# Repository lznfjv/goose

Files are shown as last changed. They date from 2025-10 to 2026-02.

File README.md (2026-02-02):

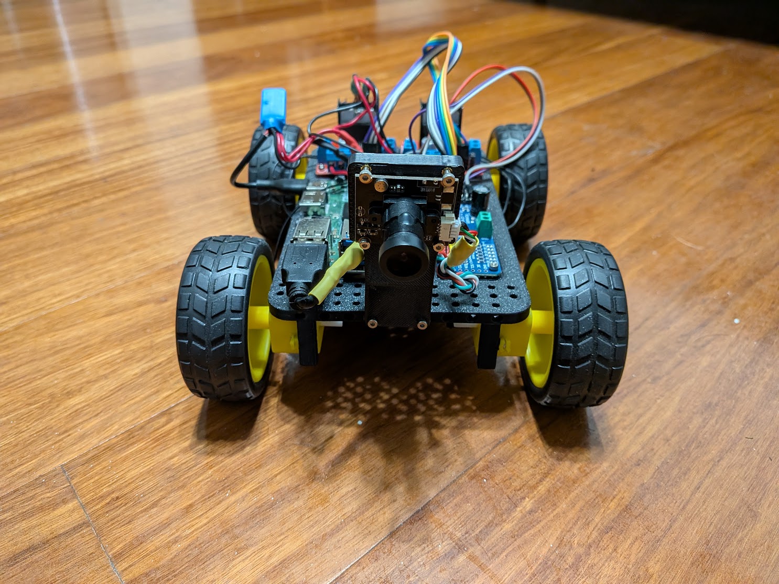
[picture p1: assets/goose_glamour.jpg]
Goose Glamour Shot


# GooseBot - A hands-on, up-to-date instructional platform for robotics
Author: Kevin Racktoo

## Problem
There is a startling lack of robotics kits on the market which effectively guide students through the process of constructing and programming a modern robot.
Sure, there are options that provide opportunities for low-level programming of servos and motors, and others that demonstrate basic computer vision filtering techniques.
However, very few kits present the opportunity to thoroughly understand every element of the modern robot. GooseBot, or simply Goose, is an in-development project, designed to be
the ideal educational robotics kit, providing experience with real-world technologies that sticks because the procedures employed are exactly those used in the real-world.

## Objective
The GooseBot project kit will encompass the following topics with the objective of creating an autonomous ground-vehicle robot which closely emulates the functionality of a self-driving car.
- Hardware selection
-   Sensors
-   Chassis
-   Mechatronics
-   Power system
- Computer vision techniques
- Hardware acceleration using NPU
- Programming control of mechatronic components
- Sensor fusion

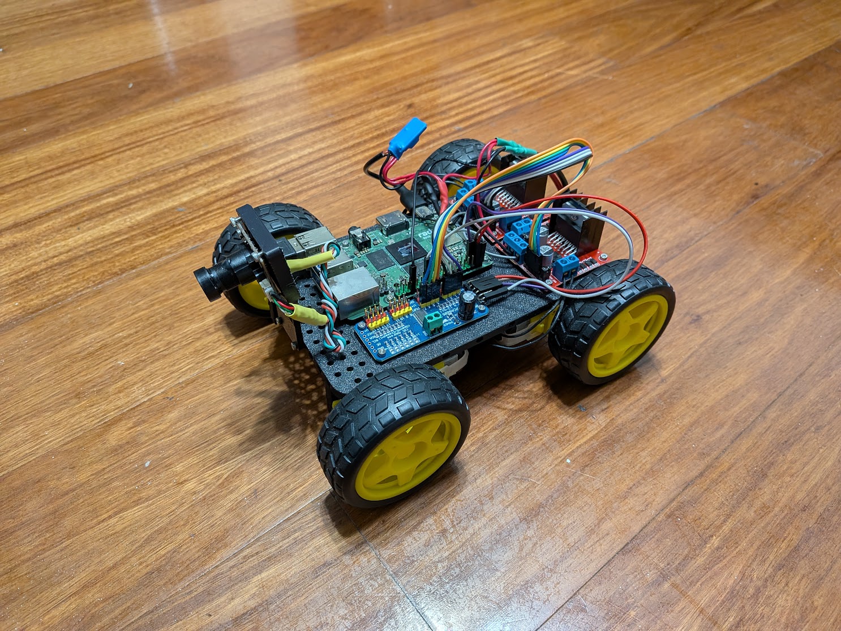
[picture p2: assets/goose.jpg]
Goose


# Progress
See the respective subsections in this repo for further information.

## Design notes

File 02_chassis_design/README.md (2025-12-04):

# Parameters
The chassis of the robot will be designed such that
- All selected components are easily mounted/unmounted
- The chassis is easily reproduced using any ordinary 3D printer
- Impact will not damage the frame
- Weight will not prevent the motors from functioning as expected
- Ventilation prevents overheating of any temperature-sensitive components

# Chassis

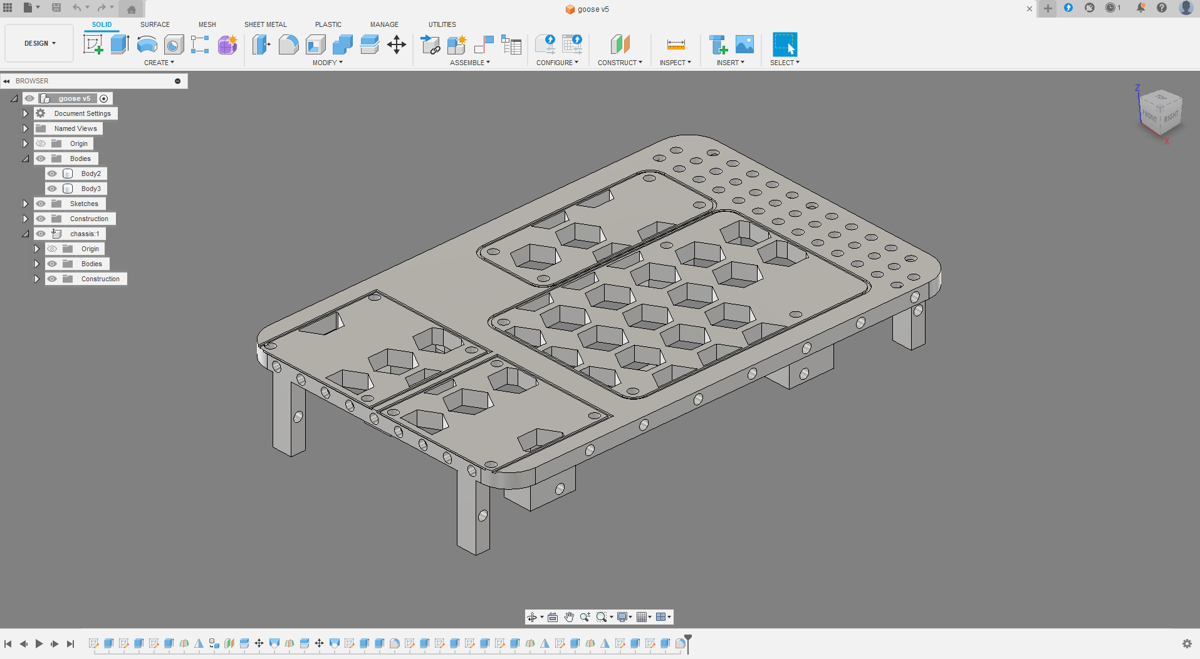
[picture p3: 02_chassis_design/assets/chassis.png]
Goose V5 Chassis


This was created in Autodesk Fusion, and designed for easy printing on most common 3D printers. I've used ASA for its strength and UV resistance, but this could just as easily be produced with ABS or even PLA. The Fusion archive file is provided for easy modification, but the STEP file should be all you need to print.

Lots of mounting holes are available, sized for M2 heat-set inserts. Heat-set inserts will allow the user to mount and unmount components as many times as they would like without worry of wearing out the threading on the 3D print itself. The inserts I use can be found here:
https://www.amazon.com/dp/B088QJG676

Each of the primary selected components has its own designated spot, with measurements taken to ensure precise mounting and no additional strain on the components.

# Camera Mount

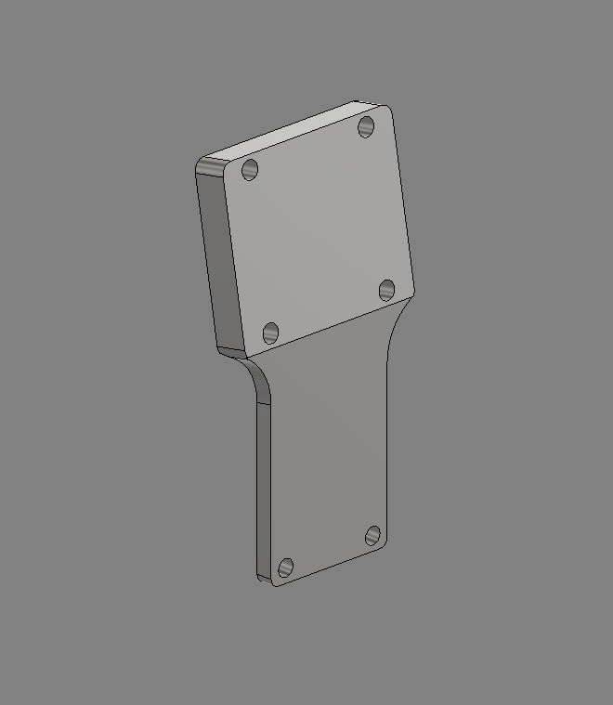
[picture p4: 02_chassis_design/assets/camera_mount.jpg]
Camera Mount


Additionally, I've provided a camera mount that was designed for the de-housed camera sensor module from the USB webcam linked in the previous chapter.

This mount is designed to be attached to the front of the Goose Chassis v5 using M2 screws and the aforementioned heat-set inserts. Heat-set inserts can also be used on the upper setion of the mount to retain the camera module, or hex nuts can be used at the rear of the mount to secure the module.

The Fusion (.f3d) archive file is provided such that you may modify the mount to fit any other camera modules if desired.

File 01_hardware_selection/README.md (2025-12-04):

# Parameters
The hardware for GooseBot is selected to meet the following parameters.

- Low cost - As this kit is to be used by students and educators, the complete bill of materials should not exceed $100 USD at the time of writing this document. As some components will be slightly lower-cost in bulk, I will allow the limit to be exceeded whenever bulk orders are cheaper or there are lower-cost alternatives available. Additionally, much of these components will already be on-hand, but the comprehensive bill of materials summary at the end of this document will include some of those, too.
- Comparable performance to DuckieBot - The DuckieBot is centered around the Nvidia Jetson Nano 4GB. The Nano *was* a capable device in its prime due to its onboard GPU, allowing for acceleration of computer vision processing using CUDA libraries. Today, many more affordable alternatives exist, utlizing Neural Processing Units (NPUs). Likewise, devices with faster processors, more memory, and wider arrays of peripherals are available. At the very least, GooseBot should be able to perform as well as DuckieBot; at best, it will perform far better.
- Up-to-date software - My greatest gripe with the DuckieBot, and with Jetson Nano's in general, is the use of completely obsolete software. Nvidia requires the use of its own customized version of Ubuntu 18.04 on the Jetson Nano as it has not updated the Linux kernel to allow hardware acceleration on its custom Tegra CPU architecture. This makes the development and modification of software on the DuckieBot a collossal pain; my Embedded Control class has spent *weeks* debugging and troubleshooting software that should be nearly plug-and-play.
- Widespread availability - The components selected should be easily purchaseable from reliable distributors such as Mouser and DigiKey. Where this is impractical, the components must be easily substitutable.

# Single-board Computer (SBC)
To meet the *comparable-performance* parameter, the single-board computer selected as the core component of GooseBot should have 
- at least 4GB of RAM (preferably the faster, higher-bandwidth LPDDR5)
- NPU with operating speed of at least 3TOPs
- WiFi to take the place of the external USB WiFi dongle used on the Jetson Nano
- USB ports for peripherals
- MicroSD expandable storage
- Common communication interfaces on GPIOs (I2C, SPI, PWM, Analog, etc.)
- Up-to-date software support (Ubuntu LTS for next two years minimum)

The SBC selected to meet these criteria is the Radxa Rock5c Lite. Its characteristics are given:
- Rockchip RK3582 hexa-core CPU
- Anywhere between 2 and 32GB of LPDDR4x RAM
- MicroSD expandable storage
- 5TOPS NPU
- Identical GPIO as the Raspberry Pi and Jetson Nano
- WiFi and Bluetooth in-built
- USB2 and USB3
- Native support for Ubuntu 20 and 22

The specific model I am using can be found here for $65, with 4GB of RAM.
https://www.amazon.com/Radxa-ROCK-5C-RK3588S2-4GB/dp/B0CYY1R9ZH

# Motors and Wheels
We want a DC motor setup for simple, effective control. Motor+gearbox assemblies almost identical to those onboard the DuckieBot are available in entire kits for <$20. This is the kit I will be using:
https://www.amazon.com/dp/B08JLYY77W

This comes with wheels, motors, gearboxes, and H-bridge motor driver modules.

# Sensors
## Camera
The foremost sensor on the platform is the camera module. Rather than a typical CSI camera module which ranges in cost from $20 to $100, a simple USB webcam with a wide field-of-view can be used, with the same or better optical performance. Furthermore, many USB webcams are coupled with onboard microphones, which enables development of audio processing features. The component selected is this:
https://www.amazon.com/dp/B0F7Y6JLM7

## Time-of-Flight
In addition to the computationally-expensive visual processing system that the robot will use, time-of-flight sensors can be employed at the front and sides of the robot for compact, resource-constrained proximity sensing and obstacle avoidance. Again, these can be found at extremely low costs. This set of three units can be had for just $10.
https://www.amazon.com/dp/B0B6ZT7NRW

# Middleware
For simplified integration of sensors and drive components, it is useful to have a PWM-I2C interface. This way, we can offload the PWM signal generation that will be used to vary speeds of the motors to a designated component, rather than having to consume valuable CPU cycles of the SBC on such a tedious, repetitive tasks. Furthermore, servos and additional PWM-driven robotic components can easily be added without regard for the limited number of PWM pins on the SBC. I'm using this board, which has numerous alternatives available from various sellers on Amazon and DigiKey. The set I purchased includes two modules, and is $10.
https://www.amazon.com/dp/B0CNVBWX2M

# Power System
We need to be able to provide adequate power to all drive components while also maintaining a continuous 5V at 2.5A for the SBC. 

## Batteries
Lithium-ion batteries are the status-quo for robotics projects like these. A 3S (11.1V nominal) LiPo will be perfect. This instance is a bit more costly than I'd like for this project, but suitable alternatives can be found at hobby shops and RC drone suppliers for even cheaper.
https://www.amazon.com/dp/B07DNQMRWW

## 5V DC/DC Converter
As the 3S battery will output just under 13V at full charge, we need to drop this down to 5V for the SBC and sensors, and regulate that voltage to prevent brown-outs. There are tons of suitable DC/DC converters available, and I happened to have a few that would do on hand. Here's a set of six such DC/DC converters for around $14, that we can adjust to output the 5V that we'll need.
https://www.amazon.com/MP1584EN-DC-DC-Converter-Adjustable-Module/dp/B01MQGMOKI

# Bill of Materials (BoM Summary)

Here are all of updated materials in a convenient table, for ordering (costs as of 12/03/2025). Some of these parts, such as assembly hardware, are optional. Additionally, many arrive as kits or sets that can be used for more than one robot. It is only assumed that the builder already possesses a 3S LiPo balance charger, wire, dupont jumper wires, a soldering station, and heatshrink/electrical tape.

| Category | Item | Specs/Notes | Cost | Source |
| :--- | :--- | :--- | :--- | :--- |
| **SBC** | **Radxa Rock5c Lite** | 4GB RAM, 5TOPS NPU, WiFi/BT | **$66.99** | [Amazon Link](https://www.amazon.com/Radxa-ROCK-5C-RK3588S2-4GB/dp/B0CYY1R9ZH) |
| **Motors** | **DC Motor Kit** | Includes wheels, gearboxes, drivers | **$15.99** | [Amazon Link](https://www.amazon.com/dp/B08JLYY77W) |
| **Sensors** | **USB Webcam** | USB connector, onboard mic | **$9.99** | [Amazon Link](https://www.amazon.com/Diccik-Webcams-Correction-FaceTime-Hangouts/dp/B0F2Z2DXW3) |
| **Sensors** | **Time-of-Flight** | Set of 3 units, prox/obstacle | **$9.99** | [Amazon Link](https://www.amazon.com/dp/B0B6ZT7NRW) |
| **Middleware**| **PWM-I2C Board** | Set of 2, Servo/Motor control | **9.99** | [Amazon Link](https://www.amazon.com/dp/B0CNVBWX2M) |
| **Power** | **3S LiPo Battery** | 11.1V Nominal | **29.69** | [Amazon Link](https://www.amazon.com/dp/B07MQT6YJN) |
| **Power** | **DC/DC Converter** | Set of 6, Adjustable (13V -> 5V) | **$12.25** | [Amazon Link](https://www.amazon.com/MP1584EN-DC-DC-Converter-Adjustable-Module/dp/B01MQGMOKI) |
| **Assembly** | **M2 Heat-set Inserts** | Optional, More convenient mounting | **$8.99** | [Amazon Link](https://www.amazon.com/dp/B088QJG676) |
| **Assembly** | **Hardware** | M2 Assorted screws | **$8.99** | [Amazon Link](https://www.amazon.com/dp/B0D3X33XGB) |
| | | **Total Estimate:** | **$172.87** | |

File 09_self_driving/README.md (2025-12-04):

Goose

# Bringing it All Together
So far, we have a severely over-powered RC car that also happens to run an object detection model. Now, we can synthesize those two featuresets into a rudimentary self-driving car algorithm.

This section assumes that you have a model town set up, with dashed yellow lane divider lines and solid white outer lane boundary lines. You can also add some red stop bar lines here and there if you want to see your robot politely pause at the stop bars before proceeding on its merry way.

The code for this lane-following system is provided for you in the drive.py script. Here, I will break down what each part of the code is doing.

**NOTE:** This is a cobbled-together lane-following and object-detection script that demonstrates an extremly basic mechanism for having a robot autonomously follow lanes. It is far, *far* from perfect, and may be observed occasionally losing its place and giving up on lane following if it encounters something it doesn't expect. Please feel free to build on this as you please, or tear it apart and start over. It is only provided to demonstrate essential capabilities and as a reference for further development.

# Script Set-up
For convenience, let's place the drive.py script in the same `yolodetect` directory we created in chapter 6. Also, make sure your `yolovenv` Python virtual environment is active, so that we know we have an environment that is set up to run object detection models on the NPU. As a refresher:

Deactivate any existing Python venv.

    deactivate

Change directory to your home folder.

    cd ~

Activate the `yolovenv` virtual environment then enter the `yolodetect` folder.

    source yolovenv/bin/activate
    cd yolodetect

Copy the `drive.py` file into this directory, if you haven't already.

We also need to install the Python packages that we previously used for motor testing, as the same packages are used by the script to maneuver the robot.

    pip install board adafruit-blinka adafruit-circuitpython-pca9685 gpiod adafruit-circuitpython-pca9685

# Run the Script
Let's run the script and see how it behaves. Before sending Goose into action, place it in the outer lane of your model town's road, in between the yellow dashed and white solid lines.

Next, make sure that the script knows where to find your RKNN model folder. Edit line 11 in `drive.py` to point to the correct model path.

To run the script:

    python drive.py

Goose should start to move, and the terminal should present you with a URL where you can view the object-detection model's hits in near-real-time. 

# Analysis
Let's go through the code. 

## Imports
Lines 1-9 are the same imports we've been using thus far, loading relevant Python packages and libraries for the peripherals we've connected, like the I2C-to-PWM bridge module.

## Config
Lines 10-18 expose some essential configuration parameters. We set the model path, then define the axis sizes for the video feed. This is pre-set to 640x480, because this is low-resolution enough for the NPU to run inferences rapidly while maintaining high enough resolution to clearly distinguish objects. The Host IP is set to `0.0.0.0` to tell the Flask web app to broadcast to the entire local network, allowing your laptop or other host machine to receive the video stream that is being produced on the Rock5c lite.

The default port of 5000 can be changed if necessary, but if you can see the video stream without issue, there's no reason to do so. If multiple robots are running on the same network, you may want to allocate unique ports such that you don't experience network connectivity issues when trying to access the stream.

## Tuning Parameters
Lines 20-25 include some parameters that **significantly** influence the performance of the lane following algorithm. 

The first of these is an RoI (region of interest) cutoff. By default, it is set to `0.65`, essentially telling the lane following algorithm to ignore any objects that are detected in the upper 65% of the video feed. This helps to prevent Goose from turning too early in response to bends that are further down the road (early apexing), or being computationally overwhelmed by all the potential detections of a larger image. You will want to adjust this parameter if you are not using the provided camera mounting bracket, or if your camera has a wider angle than anticipated.

`Kp`, `Kd`, and `BASE_SPEED` set the proportional gain, differential gain, and uninhibited forward motor throttle, respectively. The proportional and differential gains can be adjusted if turns are being taken too slowly/quickly or if overshoots and undershoots cause harmonic oscillations. Read up on PID controllers for more information.

Lines 27-30 dictate Goose's behavior when it comes across a red-line stopbar. The time for which Goose will pause, cooldown before another stopbar trigger can occur, and distance at which a stopbar can be perceived can be adjusted here.

Finally, lines 32-34 specify some base throttle characteristics. This is dependent on several factors, such as the specific motors used, battery charge, and motor driver circuitry. As DC motors stop functioning entirely below a certain power threshold, a minimum acceptable value is defined. A maximum steer ratio is also provided to prevent the robot from completely rotating in place when it only intends to perform a gradual, 45-degree turn.

## Motor Control
A motor class is defined. It utilizes the PCA library to relate different I2C messages to distinct PWM channels, thus driving the four motors in either direction (this is why we need eight signal wires to the motor drivers - one PWM signal per one motor direction).

 The motor class also defines `set_speed` and `stop` methods, to do exactly as the names suggest.

 ## Robot Control Loop
 Now, we arrive at the critical logic of the script. The control loop begins by initializing the motors and PCA module (I2C/PWM bridge).

 The robot's speed is updated at the start of each cycle of the loop. 

 The true control logic of the robot is performed by first querying the object detection model set to run on the NPU, and drawing bounding boxes around each detected and labeled object. Areas are calculated for each bounding box, and centroids are derived. 

 The algorithm then calculates its approximate trajectory based on the center of the video feed relative to the centroids of the `yellowline` and `whiteline` bounded regions. The difference between the `target` center and the actual center drives a control law, indicating positive or negative (right or left) turning, so long as the difference is over a given threshold. The threshold is applied so as to enforce a maximum acceptable deviation from the target centroid, thus preventing unwanted 'jitter' in the robot's travel path.

 Furthermore, similar area-calculating logic is employed to detect the `redline` class's presence in the RoI. If that `redline`, or stopbar, is encountered, the aforementioned stop parameters take effect to pause the operation of the robot for a given duration.

 Throughout all of this motion control, desired changes in the robot's motion are fed into an ongoing PID control loop, where the `Kp` and `Kd` parameters are employed. The results can be witnessed in the included videos, both from the perspective of an observer and from the view of the camera aboard the robot.

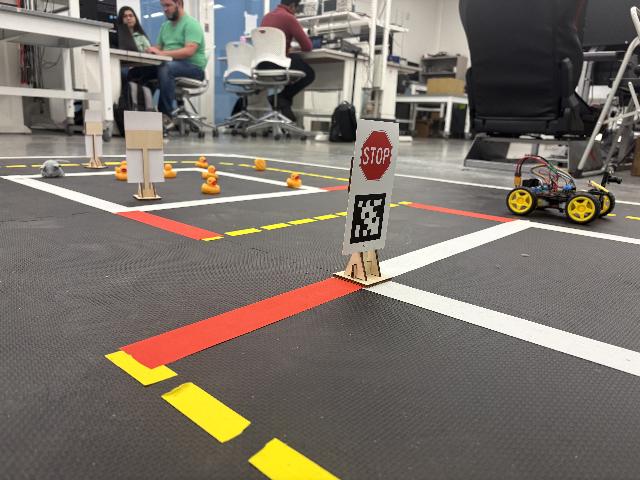
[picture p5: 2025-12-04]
07_dataset_creation/goosedataset_final/goosedataset_final/train/images/30_jpg.rf.45c1e7a9f685253ef2e2e3e0cb80889b.jpg

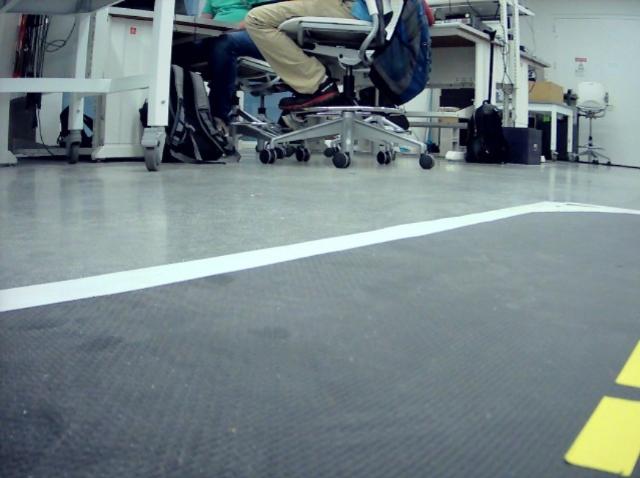
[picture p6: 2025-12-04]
07_dataset_creation/goosedataset_final/goosedataset_final/train/images/15_jpg.rf.67501fe9521fc65baefe6485deedda20.jpg

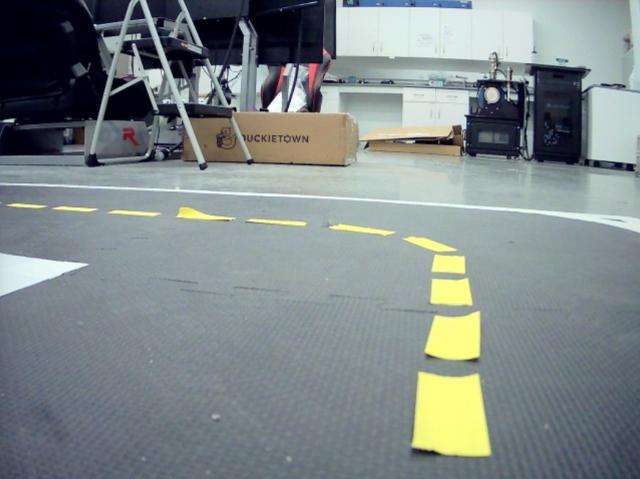
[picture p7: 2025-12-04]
07_dataset_creation/goosedataset_final/goosedataset_final/train/images/7_jpg.rf.6227b23672424cdd37b02e0d0b6905b2.jpg

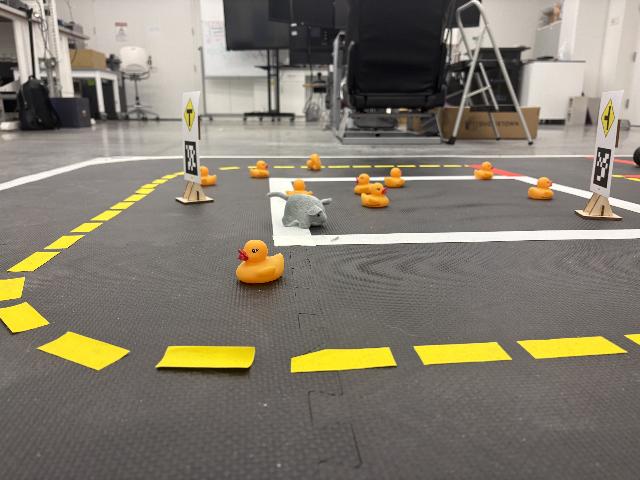
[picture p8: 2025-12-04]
07_dataset_creation/goosedataset_final/goosedataset_final/train/images/26_jpg.rf.4c52b7ff7875de6a5dc6b9cab9ed8779.jpg

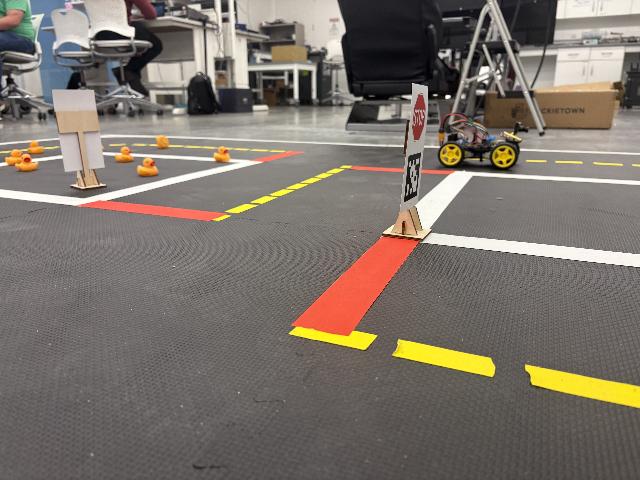
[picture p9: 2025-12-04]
07_dataset_creation/goosedataset_final/goosedataset_final/train/images/29_jpg.rf.d4b58fa7ad4b0cc9d41967ac495f9787.jpg

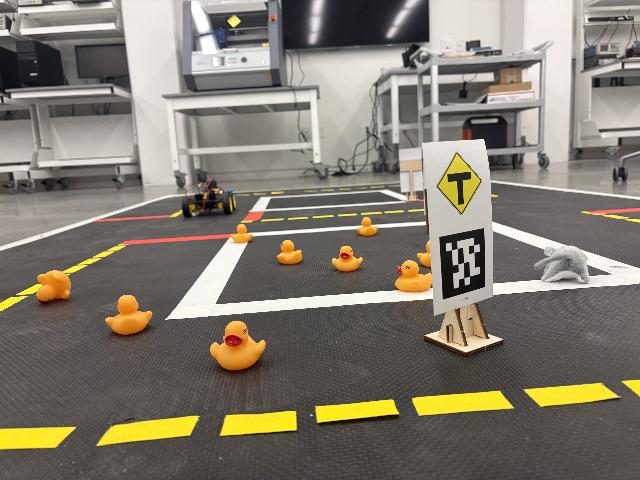
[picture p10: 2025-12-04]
07_dataset_creation/goosedataset_final/goosedataset_final/train/images/23_jpg.rf.b6fe55c9077f56e2653beb4c42d4dd4c.jpg

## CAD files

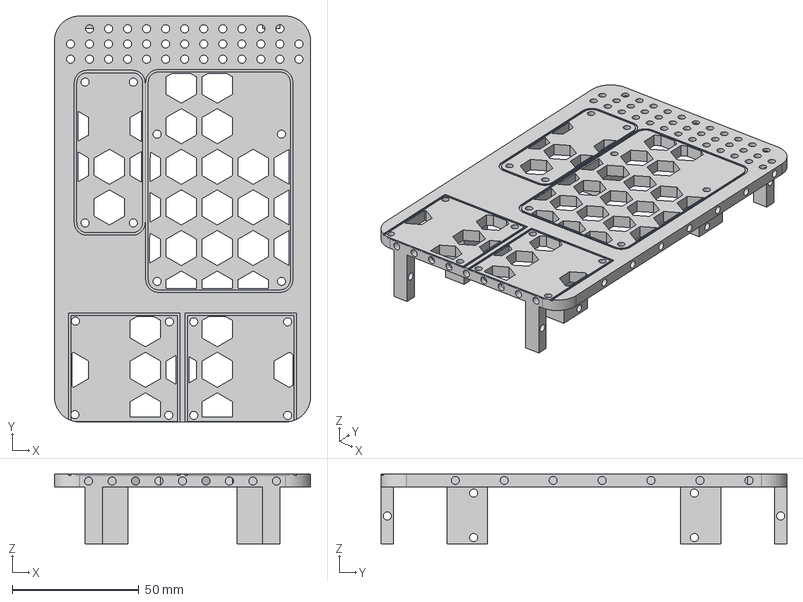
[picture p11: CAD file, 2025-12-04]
02_chassis_design/goose chassis v5.step
101.0 x 160.0 x 27.5 mm

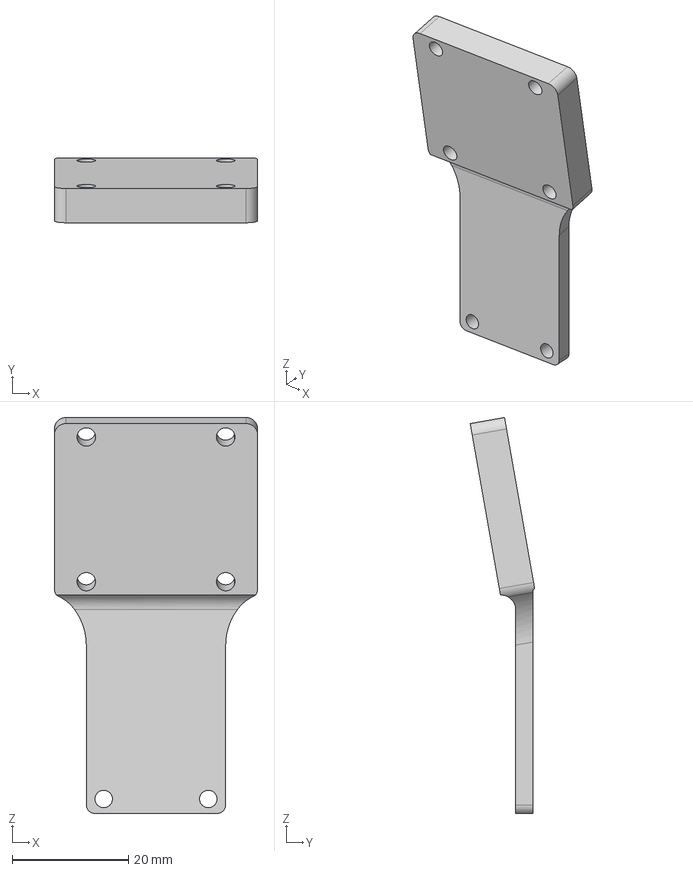
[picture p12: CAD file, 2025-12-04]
02_chassis_design/Camera Mount - Goose.step
35.0 x 11.1 x 68.2 mm

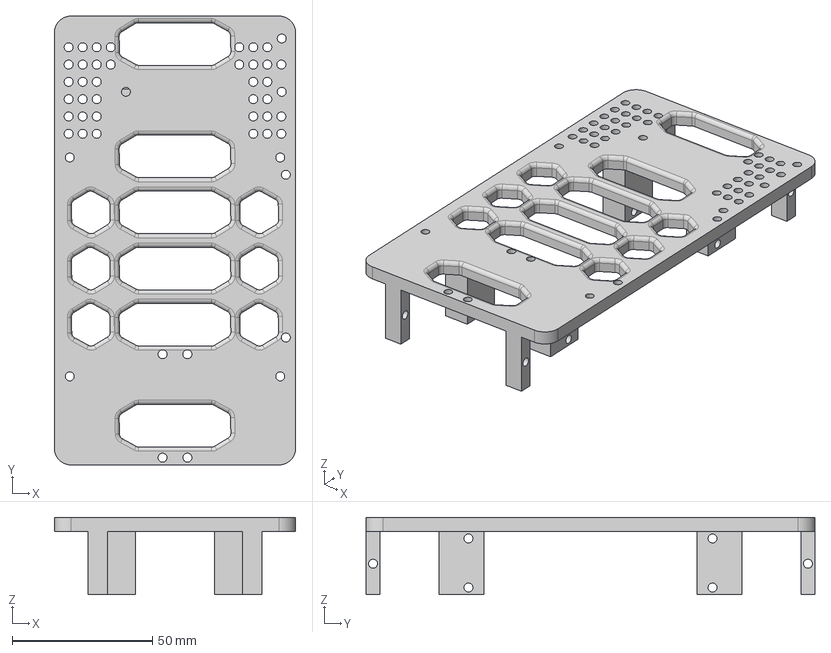
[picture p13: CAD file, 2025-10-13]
02_chassis_design/goose v4.step
86.0 x 160.0 x 27.5 mm

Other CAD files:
02_chassis_design/Camera Mount - Goose.f3d
02_chassis_design/goose chassis v5.f3d

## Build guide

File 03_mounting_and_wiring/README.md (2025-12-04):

# Wiring

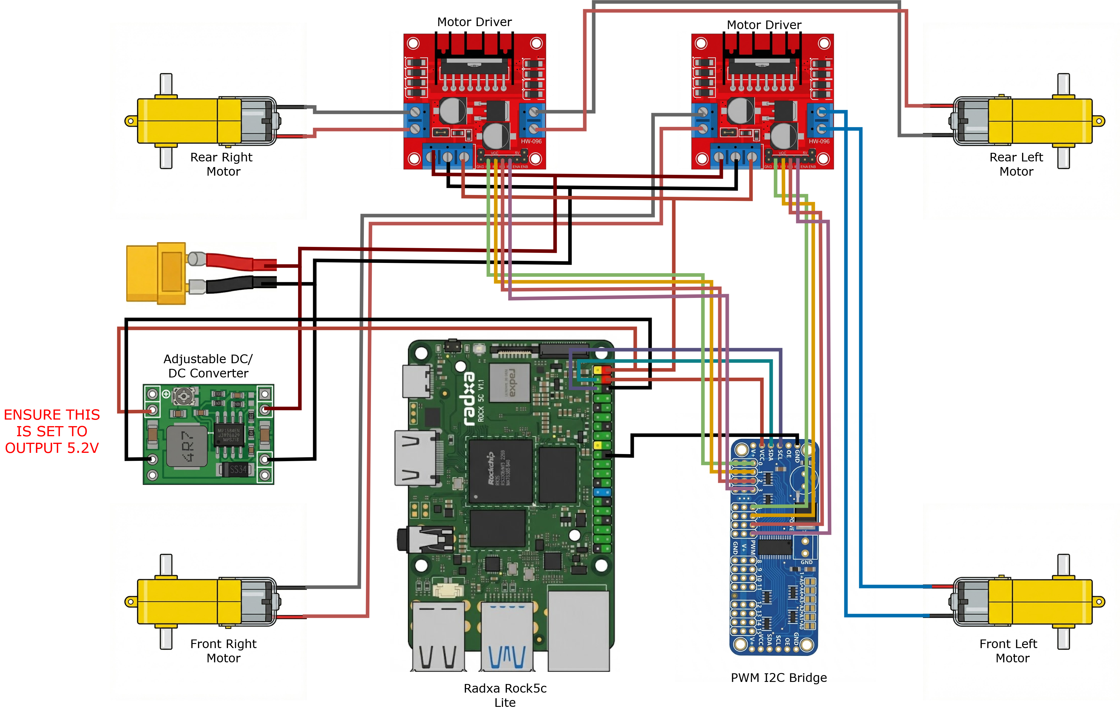
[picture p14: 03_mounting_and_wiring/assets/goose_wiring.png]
Goose V5 Wiring Diagram


Follow this wiring diagram to connect each component. Note that wires that are connected via screw terminals should be attached to their designated components *before* those components are mounted to the chassis.

# Chassis Mounting

As heat-set inserts are used to secure components to the chassis, those inserts must first be attached to the chassis using a soldering iron or other heated instrument. Myriad tutorials are available on the Internet in the use of heat-set inserts.

Each component (apart from the DC/DC converter, which can be left inline to the power cable harness) has a designated location on the chassis, marked by recessed outline.

Motor and sensor wires may be routed through the various openings in the chassis for a tidier appearance. It is advisable to cut, splice, solder, and heatshrink the webcam cable and any other cables that are excessively long so as to minimize the likelihood of cables catching upon obstacles or dragging along the ground.

# Camera Mount

Additional holes are present along the outer perimeter of the chassis as well as on the top of the front of the chassis. This is to allow flexibility in mounting locations for the camera, and adaptability for different camera sizes. The perimeter mounting holes can also be used to mount the time-of-flight sensors, although they have not yet been implemented in this instance of Goose.

# Battery Attachment
A standard 3S 2000mAh LiPo is most conveniently attached to the chassis between the sets of wheels on the underside of the chassis. A zip-tie can be routed beneath the Rock5c lite and down through the openings in the chassis to secure the battery back. Ensure that the battery's XT60 connector harness faces outwards towards the rear of the chassis to prevent the cable from obstructing the camera's line of sight.

# A note on I2C configuration
By default, the I2C bus that will be used to command the four motors may not be enabled in Radxa's operating system. To enable the specific I2C bus (there are several available on this board) that corresponds to the pins used in the above wiring diagram, follow these steps:

Login to the Rock5c lite through SSH. If connected via monitor in a desktop environment, open a terminal. Issue the following command to open the Radxa setup utility:

    sudo rsetup

Enter the administrator password when prompted and press enter. By default, the password is simply 'radxa'.

Use the arrow keys to navigate to 'Overlays' and press enter. You will be presented with a warning that changing overlays can break functionality. Select 'yes' and press enter to ignore.

Press 'enter' on 'Manage overlays'.

Use the up and down arrow keys to highlight the 'Enable I2C8-M2' option. Press SPACEBAR to select this option. An asterisk (*) should appear to the left of that option. Press ENTER to accept changes.

After changes have been applies, simply press ESC several times to exit the setup menu. A reboot is suggested before proceeding.

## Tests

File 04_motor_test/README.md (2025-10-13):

# Objective
To ensure that the motors can be used effectively, we'll make a basic script that allows us to drive the robot around using keyboard controls.

# Scripts
## Mapping
As we don't know for certain which motor is mapped to which PWM channels and which of the two channels per motor is mapped to forward and backward. a basic script is written. It allows the user to easily determine directionality of the motors and channel mapping. This script is included in this section of the repo.

## Keyboard control
The keyboard control script is included in this section of the repo.

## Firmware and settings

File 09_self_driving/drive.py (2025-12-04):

import cv2
import time
import board
import busio
import threading
from flask import Flask, Response, render_template_string
from adafruit_pca9685 import PCA9685
from ultralytics import YOLO

# --- CONFIGURATION ---
MODEL_PATH = '~/yolodetect/goose_yolo11_v1_rknn_model'
CAMERA_WIDTH = 640
CAMERA_HEIGHT = 480
CENTER_X = CAMERA_WIDTH / 2

# FLASK CONFIG
HOST_IP = '0.0.0.0'
HOST_PORT = 5000

# --- TUNING ---
ROI_VERTICAL_CUTOFF = 0.65 
Kp = 0.0007                
Kd = 0.0009 
BASE_SPEED = 0.12       
LANE_WIDTH_PIXELS = 450 

# STOP SIGN LOGIC
STOP_DURATION = 2.0        
STOP_COOLDOWN = 5.0        
STOP_THRESHOLD_Y = CAMERA_HEIGHT * 0.8 

# MOTOR PHYSICS
MIN_MOTOR_POWER = 0.07   
MAX_STEER = 0.6          

# --- GLOBAL VARIABLES FOR STREAMING ---
output_frame = None
lock = threading.Lock()

# --- FLASK APP ---
app = Flask(__name__)

# --- Motor Class ---
class Motor:
    def __init__(self, pca, in1, in2):
        self.pca = pca
        self.in1 = pca.channels[in1]
        self.in2 = pca.channels[in2]

    def set_speed(self, speed):
        if abs(speed) < 0.01:
            pwm = 0
        else:
            abs_s = abs(speed)
            mapped_speed = MIN_MOTOR_POWER + (abs_s * (1.0 - MIN_MOTOR_POWER))
            pwm = int(min(mapped_speed, 1.0) * 65535)

        if speed > 0:
            self.in1.duty_cycle = pwm
            self.in2.duty_cycle = 0
        elif speed < 0:
            self.in1.duty_cycle = 0
            self.in2.duty_cycle = pwm
        else:
            self.stop()
            
    def stop(self):
        self.in1.duty_cycle = 0
        self.in2.duty_cycle = 0

# --- ROBOT LOGIC THREAD ---
def robot_control_loop():
    global output_frame, lock
    
    # 1. Init Hardware
    try:
        i2c = busio.I2C(board.SCL, board.SDA)
        pca = PCA9685(i2c)
        pca.frequency = 100
        left_motors = [Motor(pca, 7, 6), Motor(pca, 2, 3)]
        right_motors = [Motor(pca, 5, 4), Motor(pca, 0, 1)]
    except Exception as e:
        print(f"Hardware Init Error: {e}")
        return

    def set_drive(fwd, steer):
        steer = max(min(steer, MAX_STEER), -MAX_STEER)
        left = fwd + steer
        right = fwd - steer
        max_val = max(abs(left), abs(right))
        if max_val > 1.0:
            left /= max_val
            right /= max_val
        for m in left_motors: m.set_speed(left)
        for m in right_motors: m.set_speed(right)

    def stop_all():
        for m in left_motors + right_motors: m.stop()

    # 2. Load Model
    print("Loading YOLO Model...")
    model = YOLO(MODEL_PATH)
    
    prev_error = 0
    last_stop_time = 0
    
    print("\n--- ROBOT STARTED ---")

    try:
        # Run inference
        results = model(source=0, stream=True, show=False, conf=0.5, imgsz=640, verbose=False)
        
        for result in results:
            boxes = result.boxes
            
            # --- VISION PROCESSING ---
            best_y_x = None
            best_w_x = None
            max_y_area = 0
            max_w_area = 0
            stop_requested = False
            
            current_time = time.time()
            
            for box in boxes:
                cls = model.names[int(box.cls[0])]
                x, y, w, h = box.xywh[0].tolist()
                
                # Red Line Check
                if cls == 'redline':
                    if y > STOP_THRESHOLD_Y:
                        if (current_time - last_stop_time) > STOP_COOLDOWN:
                            stop_requested = True
                
                # Lane Check (Turn Later Logic)
                cutoff_pixel = CAMERA_HEIGHT * ROI_VERTICAL_CUTOFF
                if y < cutoff_pixel: 
                    continue
                
                area = w * h
                if cls == 'yellowline' and area > max_y_area:
                    max_y_area = area
                    best_y_x = x
                elif cls == 'whiteline' and area > max_w_area:
                    max_w_area = area
                    best_w_x = x

            # --- VIDEO FRAME UPDATE ---
            # Generate the annotated frame for the web browser
            annotated_frame = result.plot()
            
            # --- CONTROL LOGIC ---
            
            # 1. Execute Stop?
            if stop_requested:
                print("!!! STOPPING !!!")
                stop_all()
                
                # Draw STOP text on frame
                cv2.putText(annotated_frame, "STOPPING FOR LINE", (50, 240), 
                            cv2.FONT_HERSHEY_SIMPLEX, 1, (0, 0, 255), 3)
                
                # Update global frame before sleeping so browser sees the message
                with lock:
                    output_frame = annotated_frame.copy()
                
                time.sleep(STOP_DURATION)
                last_stop_time = time.time()
                continue 

            # 2. Calculate Target
            if best_y_x is not None and best_w_x is not None:
                target_x = (best_y_x + best_w_x) / 2
            elif best_y_x is not None:
                target_x = best_y_x + (LANE_WIDTH_PIXELS / 2)
            elif best_w_x is not None:
                target_x = best_w_x - (LANE_WIDTH_PIXELS / 2)
            else:
                target_x = CENTER_X 
            
            # 3. PID
            error = target_x - CENTER_X
            derivative = error - prev_error
            prev_error = error
            steering = (error * Kp) + (derivative * Kd)
            
            set_drive(BASE_SPEED, steering)

            # --- VISUAL DEBUGGING ON VIDEO ---
            # Draw a Green Circle at the calculated Target X
            # Y is set to ROI Cutoff line to visually match detection area
            debug_y = int(CAMERA_HEIGHT * ROI_VERTICAL_CUTOFF) + 20
            cv2.circle(annotated_frame, (int(target_x), debug_y), 10, (0, 255, 0), -1)
            
            # Draw Center Line
            cv2.line(annotated_frame, (int(CENTER_X), 0), (int(CENTER_X), CAMERA_HEIGHT), (255, 255, 255), 1)

            # Update global frame
            with lock:
                output_frame = annotated_frame.copy()

    except Exception as e:
        print(f"Robot Loop Error: {e}")
    finally:
        stop_all()
        print("Robot Loop Ended")

# --- FLASK STREAMING FUNCTIONS ---

def generate_frames():
    global output_frame, lock
    while True:
        with lock:
            if output_frame is None:
                continue
            
            # Encode frame
            (flag, encodedImage) = cv2.imencode(".jpg", output_frame)
            if not flag:
                continue
        
        # Yield the output frame in byte format
        yield(b'--frame\r\n' b'Content-Type: image/jpeg\r\n\r\n' + 
              bytearray(encodedImage) + b'\r\n')
        
        # Limit stream framerate slightly to save bandwidth/CPU
        time.sleep(0.03) 

@app.route('/')
def index():
    return render_template_string("""
    <html>
    <head>
        <title>Robot Vision</title>
        <style>
            body { background: #111; color: #eee; text-align: center; font-family: monospace; }
            img { border: 2px solid #555; margin-top: 20px; }
        </style>
    </head>
    <body>
        <h1>RADXA ROBOT V11</h1>
        <p>Running: Stop Line + Late Turn Logic</p>
        <img src="{{ url_for('video_feed') }}" width="640" height="480">
    </body>
    </html>
    """)

@app.route('/video_feed')
def video_feed():
    return Response(generate_frames(), mimetype='multipart/x-mixed-replace; boundary=frame')

# --- MAIN ENTRY POINT ---
if __name__ == "__main__":
    # 1. Start Robot Logic in a Background Thread
    # daemon=True means this thread dies automatically if the main program quits
    t = threading.Thread(target=robot_control_loop, daemon=True)
    t.start()
    
    # 2. Start Flask Server in Main Thread
    print(f"Starting Web Server at http://{HOST_IP}:{HOST_PORT}")
    try:
        app.run(host=HOST_IP, port=HOST_PORT, debug=False, threaded=True, use_reloader=False)
    except KeyboardInterrupt:
        print("Stopping...")

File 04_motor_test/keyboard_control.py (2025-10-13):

import time
import sys
import board
import busio
from adafruit_pca9685 import PCA9685
import tty
import termios
import select

# --- Motor and Robot Configuration ---
SPEED = 0.7
# Grace period in seconds to wait for another keypress before stopping
GRACE_PERIOD = 0.3

class Motor:
    """A class to control one motor via a PCA9685 PWM driver."""
    def __init__(self, pca, in1_channel, in2_channel):
        self.pca = pca
        self.in1 = pca.channels[in1_channel]
        self.in2 = pca.channels[in2_channel]

    def set_speed(self, speed):
        """Sets the motor speed and direction from -1.0 to 1.0."""
        pwm_value = int(abs(speed) * 65535)
        if pwm_value > 65535: pwm_value = 65535
        
        if speed > 0:
            self.in1.duty_cycle = pwm_value
            self.in2.duty_cycle = 0
        elif speed < 0:
            self.in1.duty_cycle = 0
            self.in2.duty_cycle = pwm_value
        else:
            self.stop()
            
    def stop(self):
        self.in1.duty_cycle = 0
        self.in2.duty_cycle = 0

# --- Robot Movement Functions ---
def move_forward():
    print("Forward ", end="\r")
    for motor in right_motors: motor.set_speed(SPEED)
    for motor in left_motors: motor.set_speed(SPEED)

def move_backward():
    print("Backward", end="\r")
    for motor in right_motors: motor.set_speed(-SPEED)
    for motor in left_motors: motor.set_speed(-SPEED)

def turn_left():
    print("Left    ", end="\r")
    for motor in right_motors: motor.set_speed(SPEED)
    for motor in left_motors: motor.set_speed(-SPEED)

def turn_right():
    print("Right   ", end="\r")
    for motor in right_motors: motor.set_speed(-SPEED)
    for motor in left_motors: motor.set_speed(SPEED)

def stop_all():
    print("Stopped ", end="\r")
    for motor in all_motors: motor.stop()

# --- Main Program ---
if __name__ == "__main__":
    try:
        i2c = busio.I2C(board.SCL, board.SDA)
        pca = PCA9685(i2c)
        pca.frequency = 100
        
        motor_fl = Motor(pca, in1_channel=7, in2_channel=6)
        motor_fr = Motor(pca, in1_channel=5, in2_channel=4)
        motor_rl = Motor(pca, in1_channel=2, in2_channel=3)
        motor_rr = Motor(pca, in1_channel=0, in2_channel=1)
        
        all_motors = [motor_fl, motor_rl, motor_fr, motor_rr]
        right_motors = [motor_fr, motor_rr]
        left_motors = [motor_fl, motor_rl]
        
        print("All motors initialized.")
        
    except Exception as e:
        print(f"Error during setup: {e}")
        sys.exit(1)

    old_settings = termios.tcgetattr(sys.stdin)

    try:
        tty.setcbreak(sys.stdin.fileno())
        
        print("Ready for input. Press WASD to move. Press x to exit.")
        
        # Start in a known state
        current_action = stop_all
        current_action()
        last_key_time = 0

        # Main control loop
        while True:
            # Default to the current action if nothing changes
            action = current_action

            # Check if a key is pressed
            if select.select([sys.stdin], [], [], 0.05)[0]:
                key = sys.stdin.read(1)
                last_key_time = time.time()
                
                if key == 'w':
                    action = move_forward
                elif key == 's':
                    action = move_backward
                elif key == 'a':
                    action = turn_left
                elif key == 'd':
                    action = turn_right
                elif key == 'x':
                    print("\nExiting...")
                    break
                else:
                    action = stop_all
            
            # If no key has been pressed for the duration of the grace period, stop.
            elif time.time() - last_key_time > GRACE_PERIOD:
                action = stop_all
            
            # Only send a new command to the motors if the state has changed.
            if action is not current_action:
                action()
                current_action = action
        

    except KeyboardInterrupt:
        print("\nExiting...")
        
    finally:
        stop_all()
        termios.tcgetattr(sys.stdin, termios.TCSADRAIN, old_settings)
        print("\nProgram finished.")

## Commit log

2025-09-09 slim down for just motor control test
2025-10-13 Update chassis_design readme, add step file
    [goose v4.step]
2025-10-13 Add goose v4 chassis image link to chassis readme
2025-10-13 Add UNDER CONSTRUCTION README to mounting and wiring section
2025-10-13 Add readme for motor test. Add motor mapping script. Add keyboard control script
2025-10-13 Rename chapter folders to indicate order in which they occur
    [goose v4.step]
2025-12-04 Update hardware selection with more comprehensive BoM and summary table
2025-12-04 Modify chassis_design chapter to include chassis v5 model, updated images, f3d archive files, and a camera mounting bracket
    [Camera Mount - Goose.f3d, Camera Mount - Goose.step, goose chassis v5.f3d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]
2025-12-04 Add wiring diagram. Add mounting and I2C config description in chapter 3
2025-12-04 Modify chapter 4 instructions to include motor driver libraries. Write comprehensive analysis of drive.py self-driving algorithm. Include example drive.py self driving algorithm code
2025-12-04 Try to add circuit video to chapter 9 readme
